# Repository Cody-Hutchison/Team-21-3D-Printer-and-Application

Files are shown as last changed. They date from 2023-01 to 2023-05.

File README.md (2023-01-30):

# Team-21-3D-Printer-and-Application

Currently 3D Printers require users to manually upload a G-code file by and external storage device and initiate the printing process via controls on the printer. Our goal is to create a 3D printer that you ance upload, control, initiate, and interupt the 3D printing process from anywhere in the world that you have internet access. We also want to keep the print time be within 10% of the printing time of the Ender 3 which is the frame and mechanical hardware used for our printer. To try to increase the print time we are going to attempt it by speading up the Z-axis movement speed.

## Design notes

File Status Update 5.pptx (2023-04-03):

## Team 21: 3D Printer and Application Interface Bi-Weekly Update 5 Cody Hutchison Steven Liu Abigail Morar Sponsor: Dalton Cyr TA: Milenka Gamero

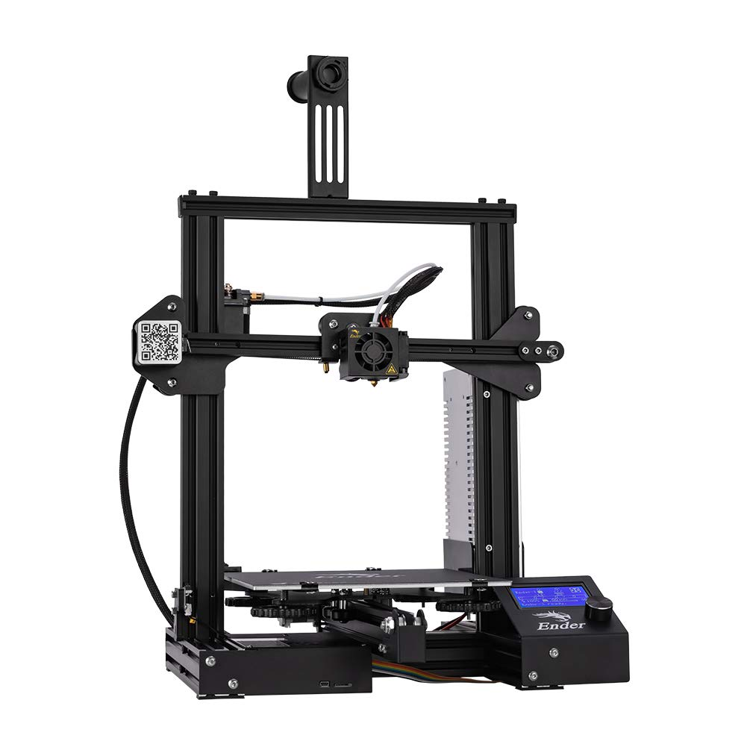
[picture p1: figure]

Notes: Michelle

## Project Summary

- Current 3D printers require the user to manually upload a G-code file by an external storage device and initiate the printing process via controls on the printer
- The new 3D printer and Application will allow the uploading, controlling, and initiation of printing from anywhere with internet access. The print time will also be within 10% of the Ender 3 printing time while also attempting to speed up the Z-axis movement speed.

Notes: Kyle

## Project/Subsystem Overview

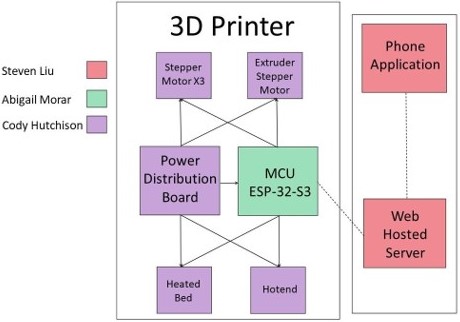
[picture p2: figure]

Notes: Eric

## Project Changes for 404

Everything is still on track from what was planned in 403.
As of now, changes are mostly geared towards fixing bugs in the subsystems for full integration, and dealing with whatever problems may arise from that.

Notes: Eric

## Project Timeline

Validate System

Finish Subsystems

Integrate Subsystems

Final Presentation

Final Demo

April 24

February 15

March 29

April 10

March 15

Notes: January 30th - February 5th
Ensure all parts required to complete PCBs are on hand or order more
Start populating PCB if they have arrived
February 6th - 12th
Have PCB populated and validate

## Electrical Subsystem Cody Hutchison

Accomplishments since last update 24 hrs of effort | Ongoing progress/problems and plans until the next presentation
| Integrate PCB with MCU Build printer case for PCBs Solder jumper wires and modify board for the axis switches

## Electrical Subsystem Cody Hutchison

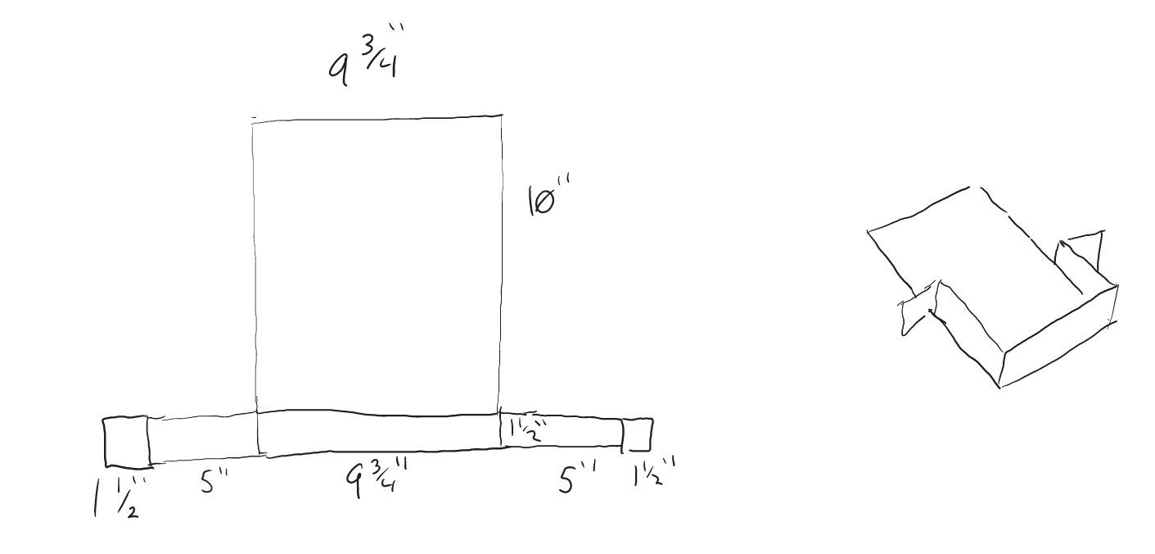
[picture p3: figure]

## Application and Server Subsystem Steven Liu

Accomplishments since last update 15 hrs of effort | Ongoing progress/problems and plans until the next presentation
Application tuning Added logo and splash screen | Look for possible improvements Finish poster Update Final Report

## Application and Server Subsystem Steven Liu

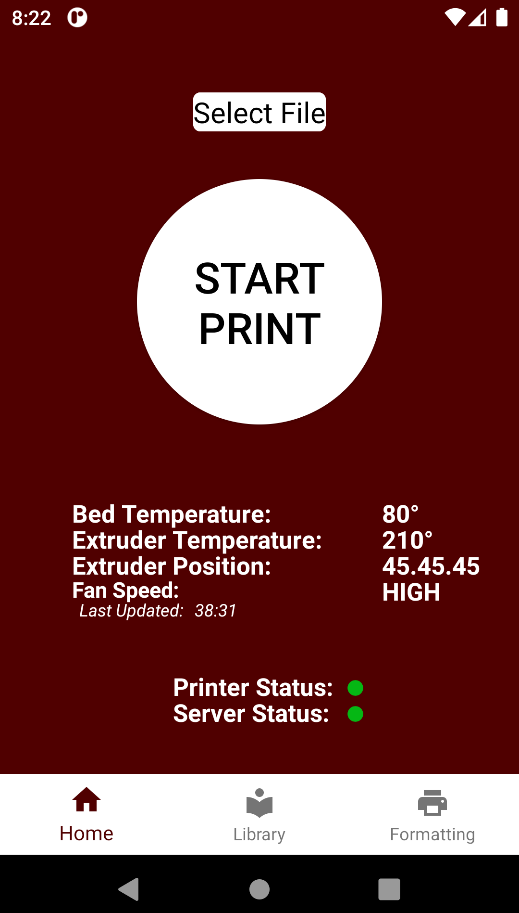
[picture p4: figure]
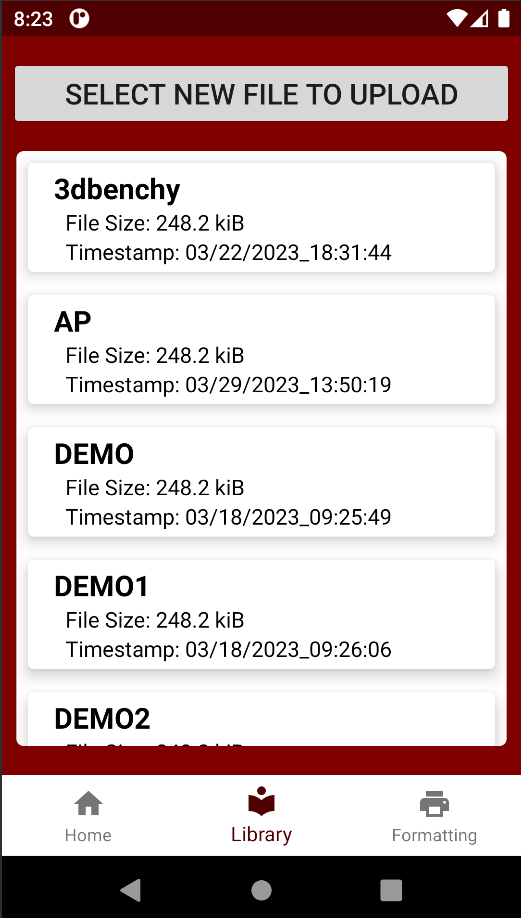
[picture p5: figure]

## Microcontroller Programming Subsystem Abigail Morar

Accomplishments since last update 20 hrs of effort | Ongoing progress/problems and plans until the next presentation
- Heated bed reading/writing and maintaining temperature correctly - Found steps per full revolution for each motor - Found mm per full revolution and steps/mm | - Measure/calculate constants for hotend - Verify all motor speeds for print and extruding amount per mm with filament - Updating changes to main code - Tweaking for accuracy

## Microcontroller Programming Subsystem Abigail Morar

## Integration

Accomplishments since last update | Ongoing progress/problems and plans until the next presentation
Continue integration between MCU and Electrical Subsystem | Validate App/Server and MCU integration Validate MCU and Electrical Subsystem integration

## Parts Ordering Status

- No parts on order or required at the moment

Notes: Michelle

## Execution Plan

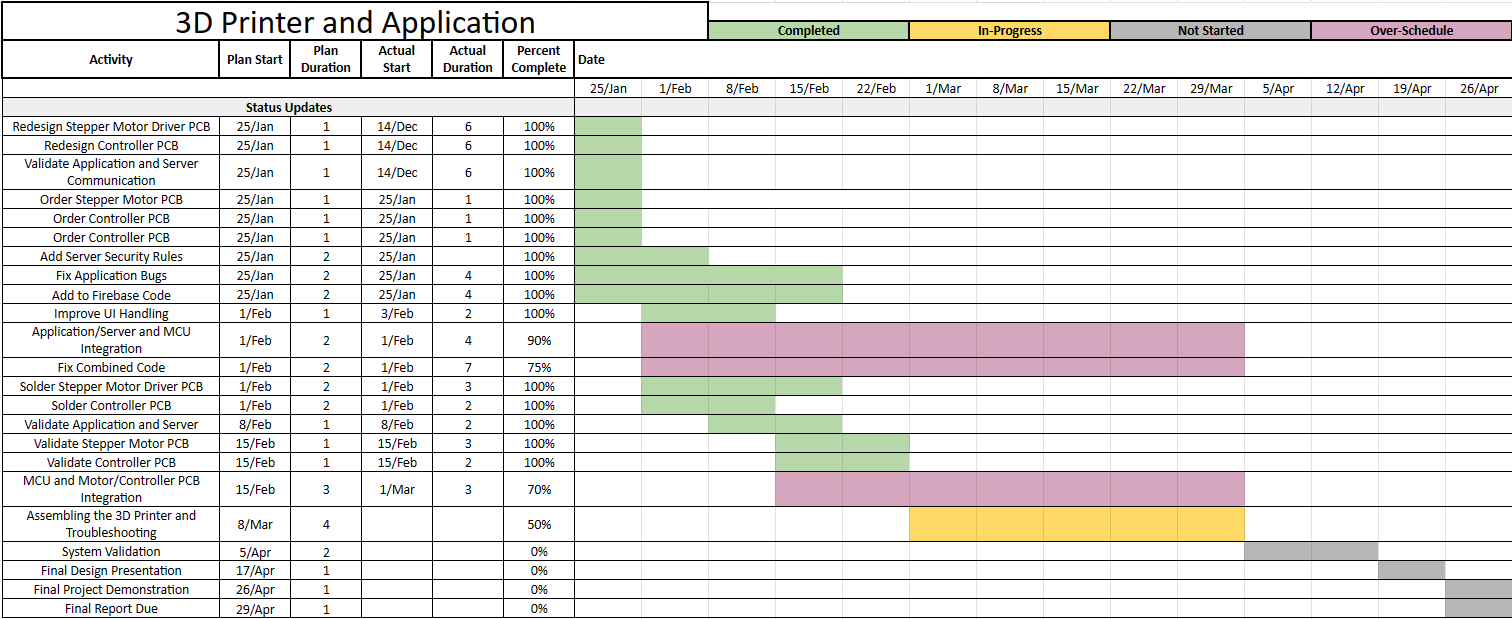
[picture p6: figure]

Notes: Michelle

## Validation Plan

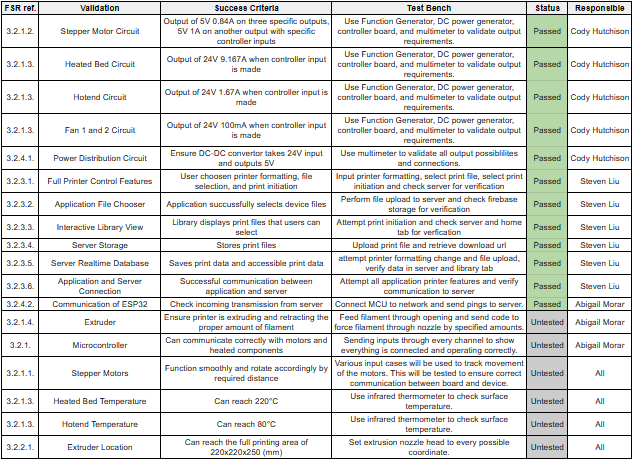
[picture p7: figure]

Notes: Michelle

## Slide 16

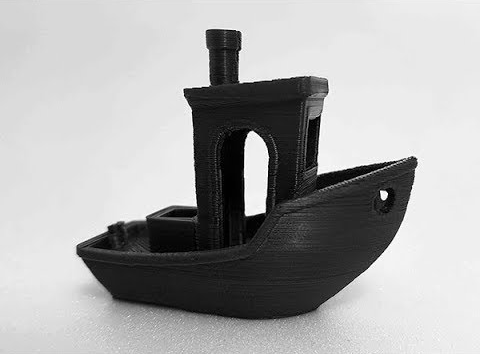
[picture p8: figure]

Questions? Comments?
Thank You

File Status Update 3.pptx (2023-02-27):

## Team 21: 3D Printer and Application Interface Bi-Weekly Update 3 Cody Hutchison Steven Liu Abigail Morar Sponsor: Dalton Cyr TA: Milenka Gamero


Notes: Michelle

## Project Summary

- Current 3D printers require the user to manually upload a G-code file by an external storage device and initiate the printing process via controls on the printer
- The new 3D printer and Application will allow the uploading, controlling, and initiation of printing from anywhere with internet access. The print time will also be within 10% of the Ender 3 printing time while also attempting to speed up the Z-axis movement speed.

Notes: Kyle

## Project/Subsystem Overview


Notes: Eric

## Project Changes for 404

Everything is still on track from what was planned in 403.
As of now, changes are mostly geared towards fixing bugs in the current subsystems, preparing for full integration, and dealing with whatever problems may arise from that.

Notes: Eric

## Project Timeline

Validate System

Finish Subsystems

Integrate Subsystems

Final Presentation

Final Demo

April 24

February 15

March 29

April 10

March 15

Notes: January 30th - February 5th
Ensure all parts required to complete PCBs are on hand or order more
Start populating PCB if they have arrived
February 6th - 12th
Have PCB populated and validate

## Electrical Subsystem Cody Hutchison

Accomplishments since last update 22 hrs of effort | Ongoing progress/problems and plans until the next presentation
- Validated Main Controller PCB - Validated Axis Driver PCB | Integrate PCB with MCU Design printer mount for PCBs

## Electrical Subsystem Cody Hutchison

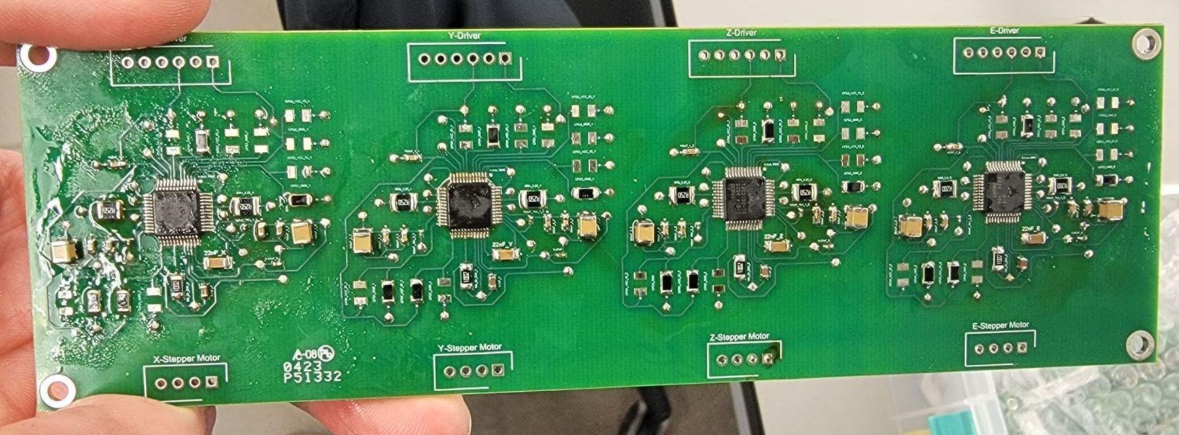
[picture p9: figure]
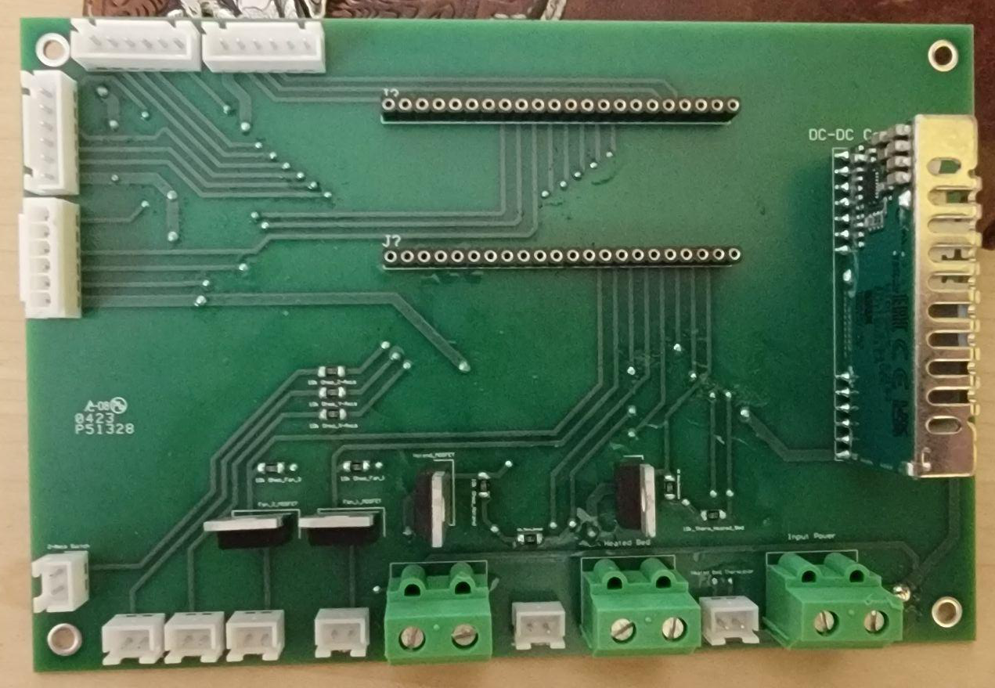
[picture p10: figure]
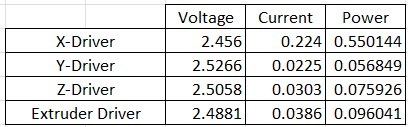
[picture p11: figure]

## Application and Server Subsystem Steven Liu

Accomplishments since last update 10 hrs of effort | Ongoing progress/problems and plans until the next presentation
Fixed url firebase communication bug Fixed in-app fragment communication bugs | Add a print completion notification to user Make a new demo recording using app from physical device Look for other possible bugs or UI improvements

## Application and Server Subsystem Steven Liu

## Microcontroller Programming Subsystem Abigail Morar

Accomplishments since last update 11 hrs of effort | Ongoing progress/problems and plans until the next presentation
- Completed integration with Firebase | - Will begin testing functionality of stepper motors and integrate with PCB

## Integration

Accomplishments since last update | Ongoing progress/problems and plans until the next presentation
App/Server and MCU subsystems integrated | Validate App/Server and MCU integration Begin integration between MCU and Electrical Subsystem

## Parts Ordering Status

- 3 TMC-2130 Driver Controller were ordered and received

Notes: Michelle

## Execution Plan

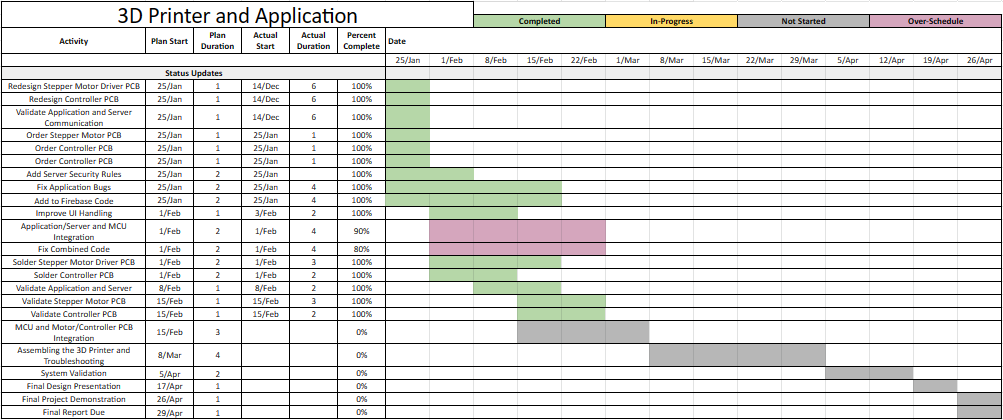
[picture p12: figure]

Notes: Michelle

## Validation Plan


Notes: Michelle

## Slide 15


Questions? Comments?
Thank You

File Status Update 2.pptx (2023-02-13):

## Team 21: 3D Printer and Application Interface Bi-Weekly Update 2 Cody Hutchison Steven Liu Abigail Morar Sponsor: Dalton Cyr TA: Milenka Gamero


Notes: Michelle

## Project Summary

- Current 3D printers require the user to manually upload a G-code file by an external storage device and initiate the printing process via controls on the printer
- The new 3D printer and Application will allow the uploading, controlling, and initiation of printing from anywhere with internet access. The print time will also be within 10% of the Ender 3 printing time while also attempting to speed up the Z-axis movement speed.

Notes: Kyle

## Project/Subsystem Overview


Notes: Eric

## Project Changes for 404

Everything is still on track from what was planned in 403.
As of now, changes are mostly geared towards fixing bugs in the current subsystems, preparing for full integration, and dealing with whatever problems may arise from that.

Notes: Eric

## Project Timeline

Validate System

Finish Subsystems

Integrate Subsystems

Final Presentation

Final Demo

April 24

February 15

March 29

April 10

March 15

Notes: January 30th - February 5th
Ensure all parts required to complete PCBs are on hand or order more
Start populating PCB if they have arrived
February 6th - 12th
Have PCB populated and validate

## Electrical Subsystem Cody Hutchison

Accomplishments since last update 12 hrs of effort | Ongoing progress/problems and plans until the next presentation
- Assembling PCBs | Validate both PCBs Integrate PCB with MCU Design printer mount for PCBs

## Electrical Subsystem Cody Hutchison

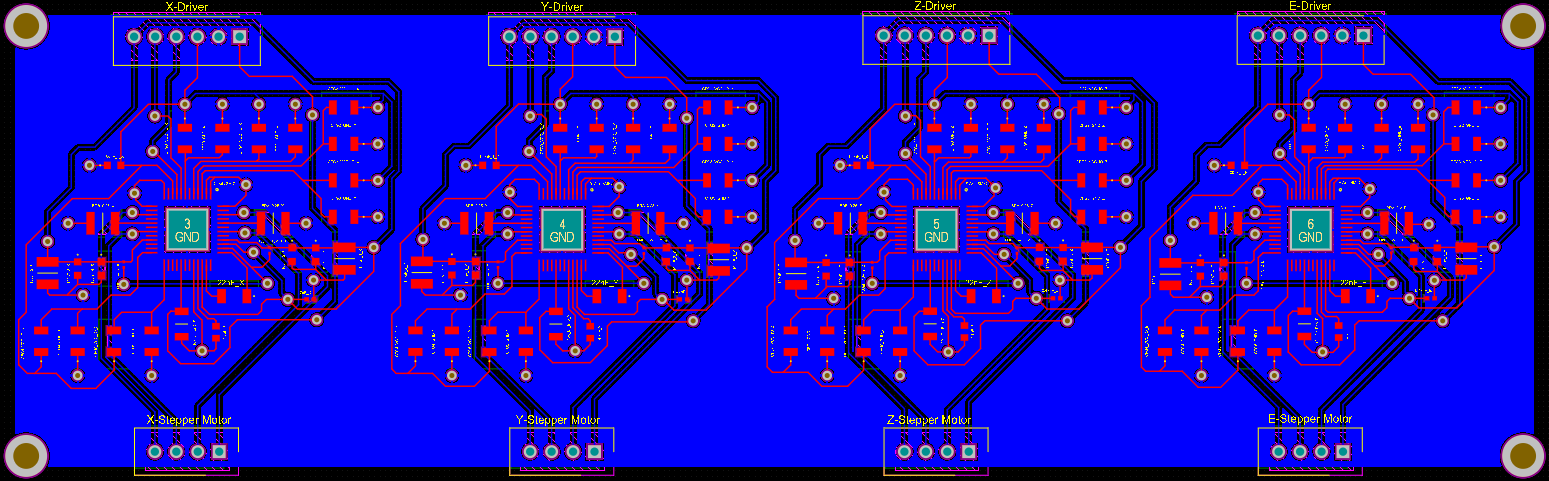
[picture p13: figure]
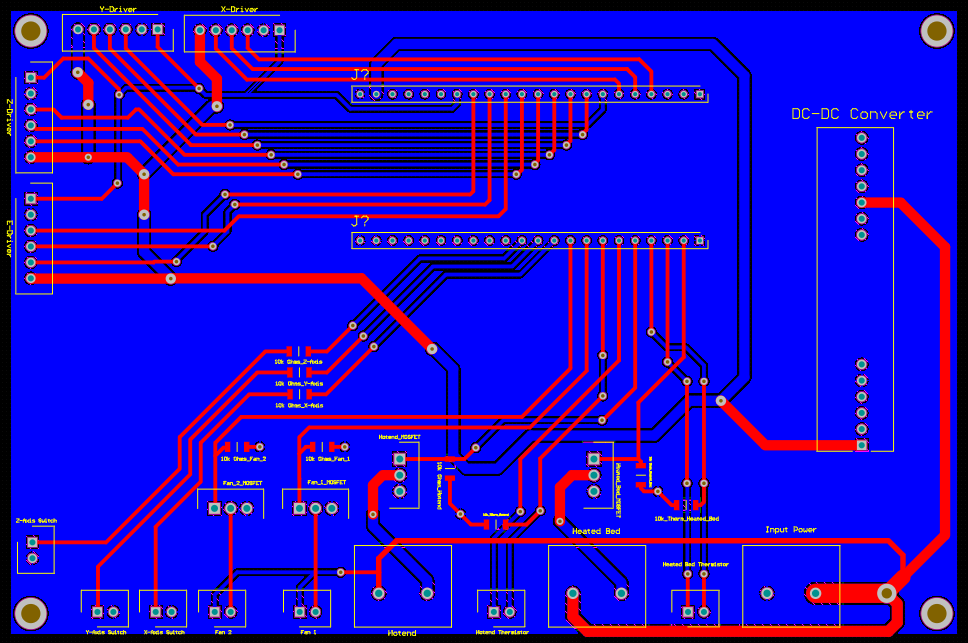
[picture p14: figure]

## Application and Server Subsystem Steven Liu

Accomplishments since last update 25 hrs of effort | Ongoing progress/problems and plans until the next presentation
- Fixed display bug using Android SharedViewModel class - Fixed bug that would freeze and crash app on file upload cancellation - Working on using Firebase Functions to work around url communication bug | - Be ready for adjustments while integrating MCU - Fix url firebase communication bug - Look for other possible bugs or UI improvements

## Application and Server Subsystem Steven Liu

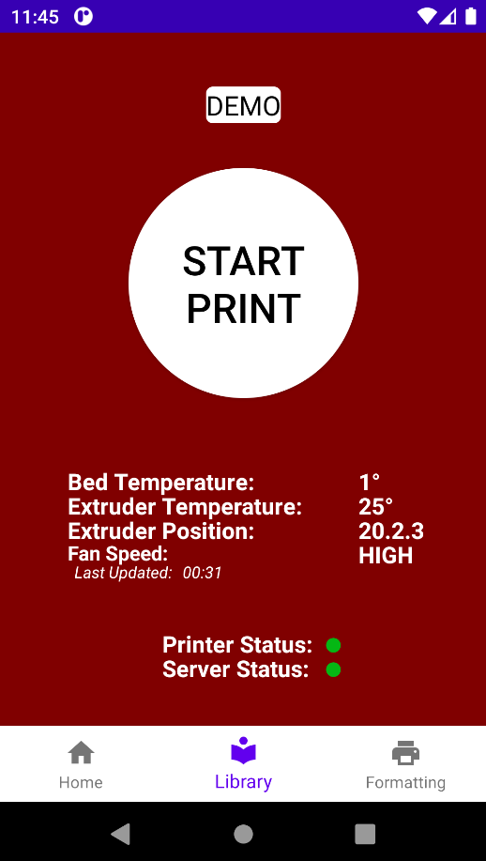
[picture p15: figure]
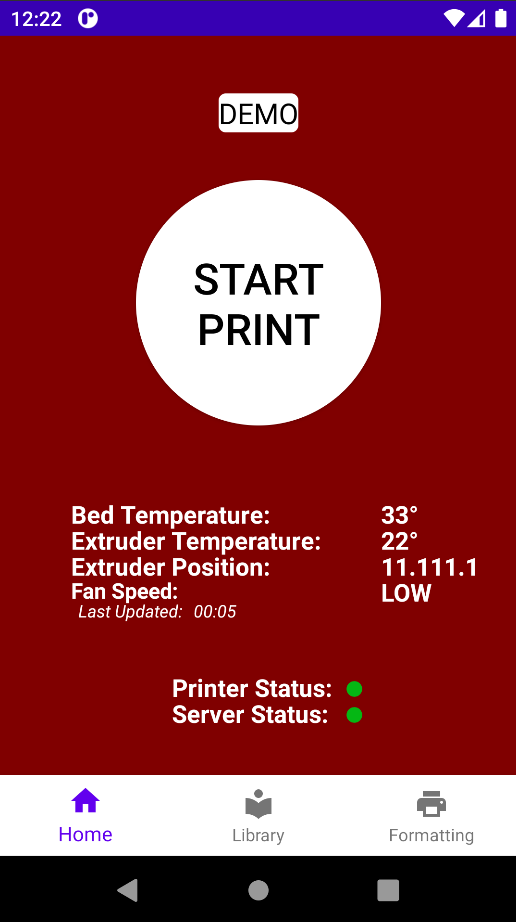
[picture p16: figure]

Display Bug Fixed

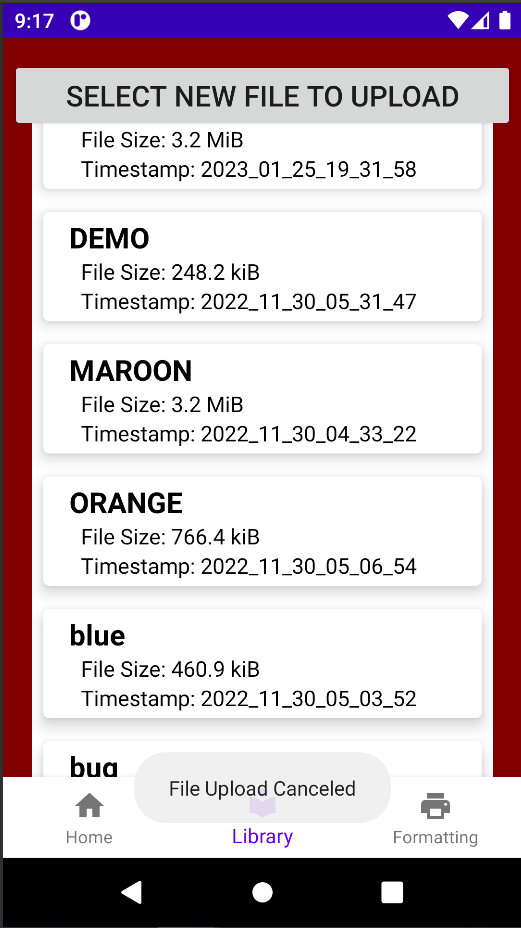
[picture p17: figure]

Cancel Upload Bug Fixed

Display Bug

## Microcontroller Programming Subsystem Abigail Morar

Accomplishments since last update 12 hrs of effort | Ongoing progress/problems and plans until the next presentation
- Began integration with Firebase server - Can write to correct path in Firebase | - Finishing up integration with the server to validate phone app communication - Will begin testing functionality of stepper motors and other components

## Parts Ordering Status

- All planned parts have been ordered and received

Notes: Michelle

## Execution Plan

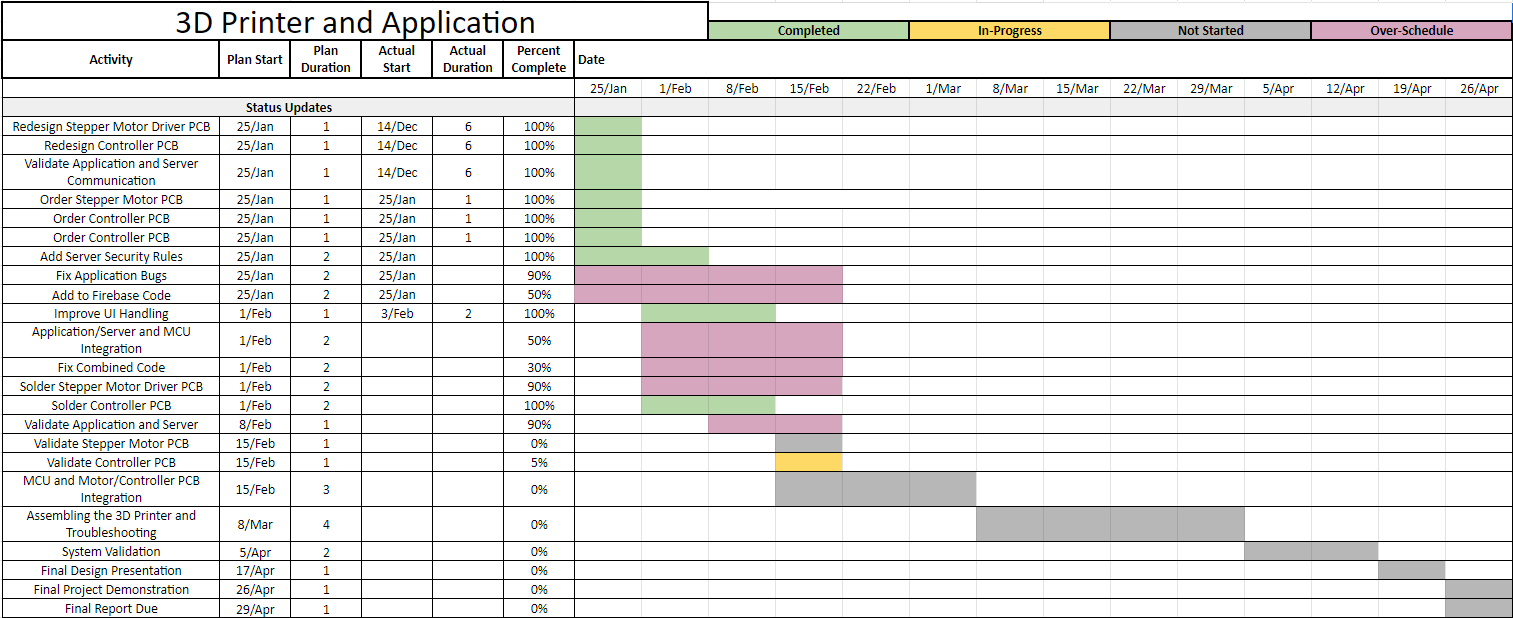
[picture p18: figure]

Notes: Michelle

## Validation Plan

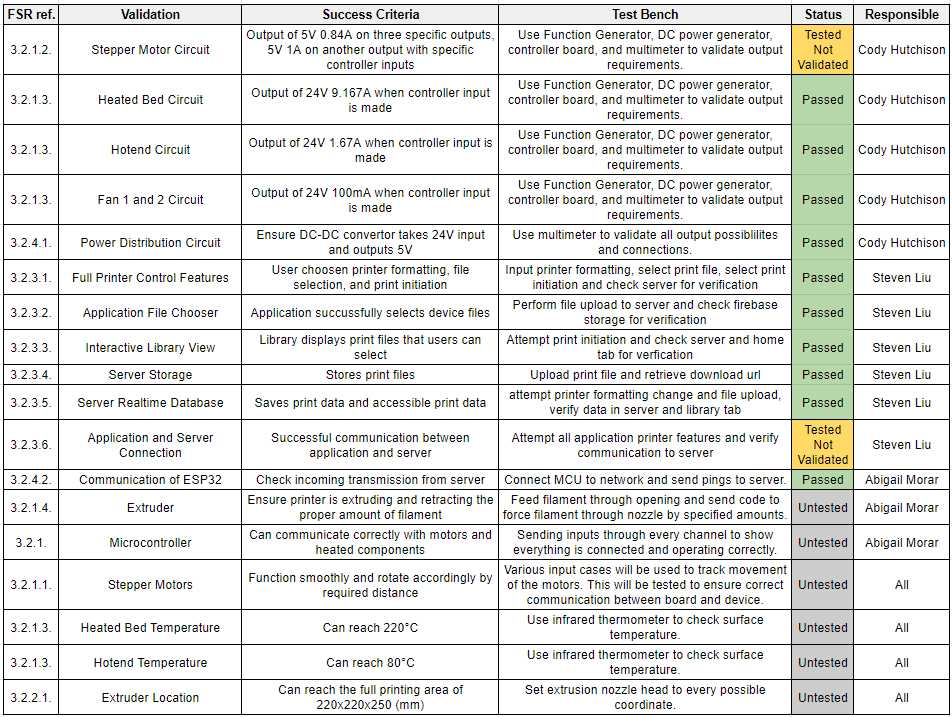
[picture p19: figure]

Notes: Michelle

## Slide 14


Questions? Comments?
Thank You

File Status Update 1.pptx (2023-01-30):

## Team 21: 3D Printer and Application Interface Bi-Weekly Update 1 Cody Hutchison Steven Liu Abigail Morar Sponsor: Dalton Cyr TA: Milenka Gamero


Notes: Michelle

## Project Summary

- Current 3D printers require the user to manually upload a G-code file by an external storage device and initiate the printing process via controls on the printer
- The new 3D printer and Application will allow the uploading, controlling, and initiation of printing from anywhere with internet access. The print time will also be within 10% of the Ender 3 printing time while also attempting to speed up the Z-axis movement speed.

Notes: Kyle

## Project/Subsystem Overview


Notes: Eric

## Project Changes for 404

Everything is still on track from what was planned in 403.
As of now, changes are mostly geared towards fixing bugs in the current subsystems, preparing for full integration, and dealing with whatever problems may arise from that.

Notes: Eric

## Project Timeline

Validate System

Finish Subsystems

Integrate Subsystems

Final Presentation

Final Demo

April 24

February 15

March 29

April 10

March 15

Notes: January 30th - February 5th
Ensure all parts required to complete PCBs are on hand or order more
Start populating PCB if they have arrived
February 6th - 12th
Have PCB populated and validate

## Electrical Subsystem Cody Hutchison

Accomplishments since 403 55 hrs of effort | Ongoing progress/problems and plans until the next presentation
- Redesigned and corrected errors with the the Stepper Motor Driver PCB. - Minor modifications to the Controller PCB due to a header component used to plug the MCU being incorrect - Placed order for new PCB boards | - Populate both PCBs - Validate both PCBs

## Electrical Subsystem Cody Hutchison

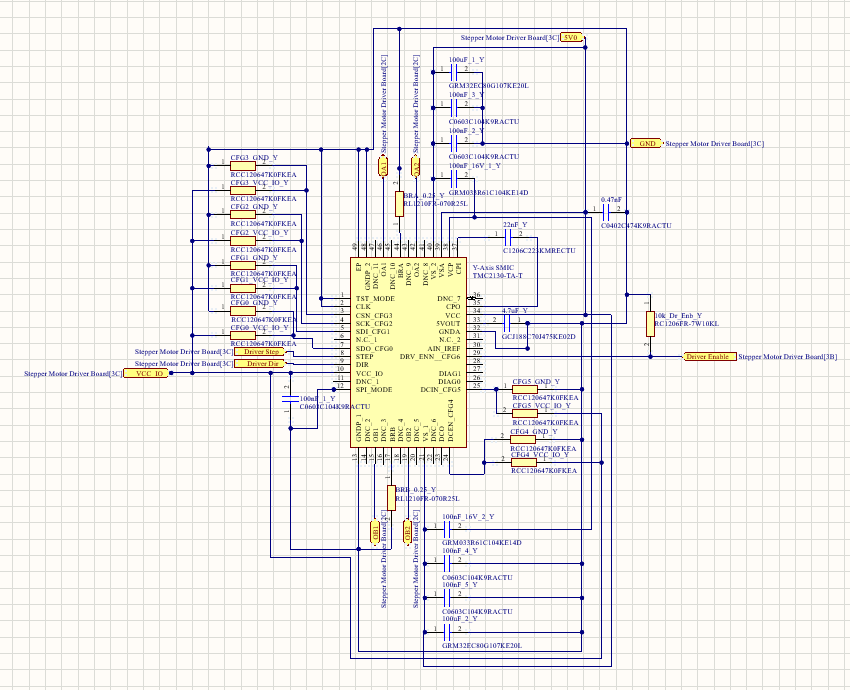
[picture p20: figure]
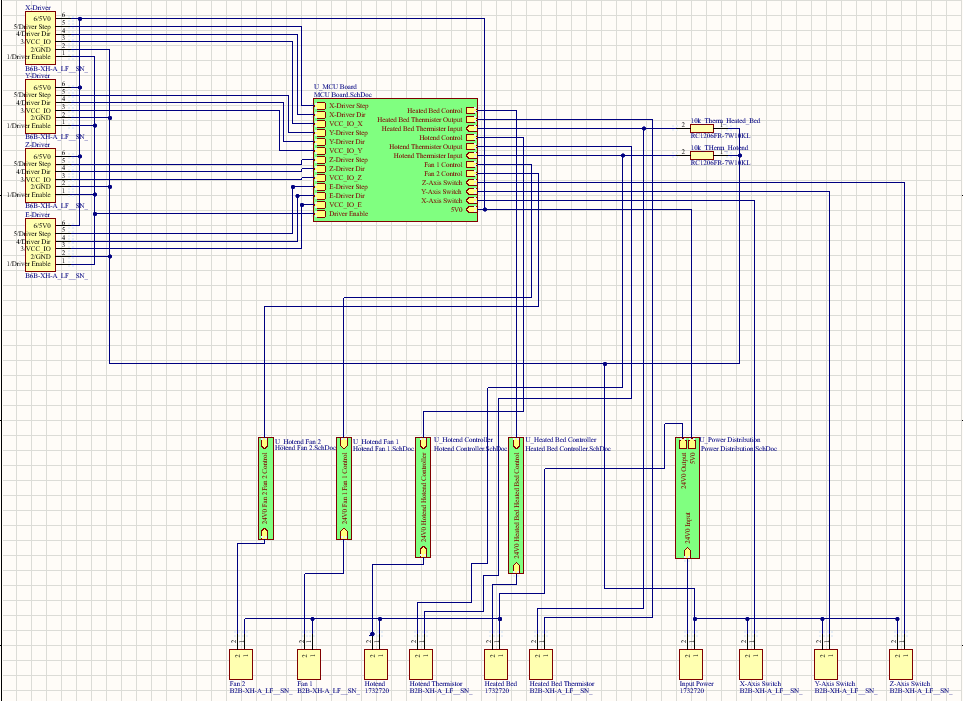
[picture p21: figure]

## Application and Server Subsystem Steven Liu

Accomplishments since 403 15 hrs of effort | Ongoing progress/problems and plans until the next presentation
- Added security rules to server - Improved application UI - Incorporating Android SharedViewModel class to fix bug | - Finish incorporating SharedViewModel class to app and validate - Work on fixing other bug - Find other possible UI improvements - Work on connecting with MCU subsystem

## Application and Server Subsystem Steven Liu

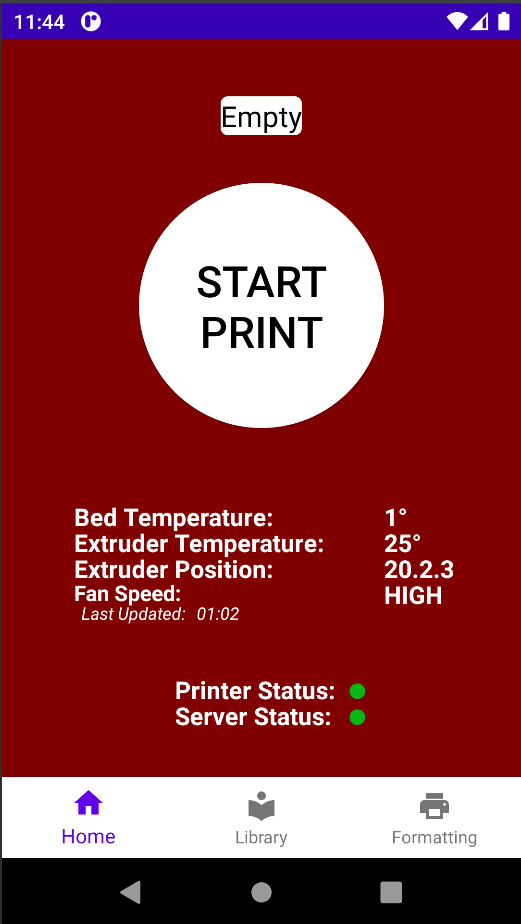
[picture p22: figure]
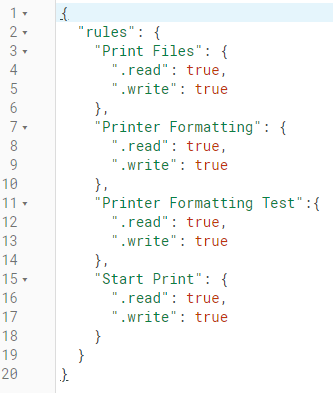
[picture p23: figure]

## Microcontroller Programming Subsystem Abigail Morar

Accomplishments since 403 10 hrs of effort | Ongoing progress/problems and plans until the next presentation
- Ensured all code still works and can connect to server - Combined code | - Fix bug with reading from Firebase and other issues - Adding code to check for updates from phone app to interrupt G-code reading process, update, then resume or cancel - Waiting on integration with motors to calculate the steps to mm

## Parts Ordering Status

  - PCBs are currently on order
  - Order PCB components

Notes: Michelle

## Execution Plan

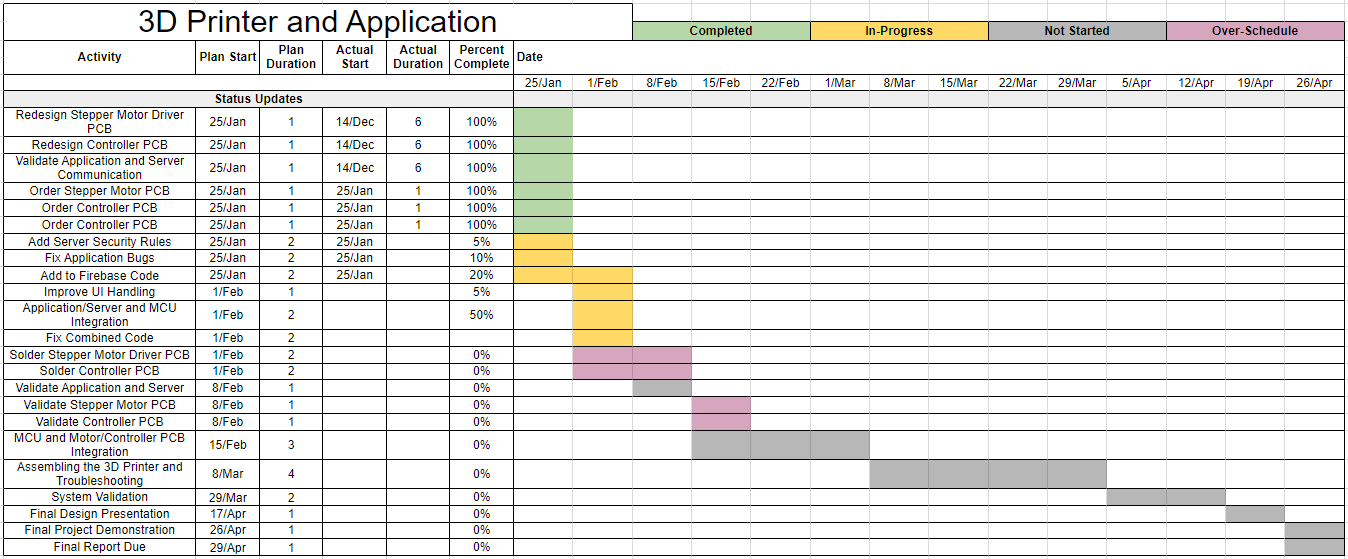
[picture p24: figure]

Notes: Michelle

## Validation Plan


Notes: Michelle

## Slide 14


Questions? Comments?
Thank You

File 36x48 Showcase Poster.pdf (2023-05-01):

### Outcomes

The printer communicates to the phone application via Wi-Fi and can be controlled remotely by the user. Control from the app includes setting extruder location, fan power, and heated bed and hotend temperatures. The MCU executes these commands and sends updates back to the app for real-time user verification. The application parses and uploads G-code files to the database as well provides user ability to start and cancel prints. The PCBs currently work as expected. This is the 2nd iteration of the designs and had to make a few minor corrections on main controller board by soldering wires as jumpers and isolating 3 separate pins from the ground plane.

### Engineering Analysis

The mobile application, server, and MCU work together to provide an intuitive user interface and allow remote communication. While the MCU and PCB work together to perform all physical operations of the 3D printer. All user inputs are communicated from the application to the server, which provides a database and storage for handling all pertinent information that can then be read by the MCU. The stepper motor controller PCB provides control over the stepper motors on the 3D printer.

# 3D Printer and Phone Application

## Cody Hutchison, Steven Liu, Abigail Morar Dalton Cyr

Current | Issues

The 3D printer will run through the G-code and attempt to print an item, but is currently only printing on one quadrant of the heated bed. Another part of the issue is the extruder isn’t pushing enough filament out to properly print.

Figure 1. 3D Printer System Overview

### Problem Definition

Current 3D printers require the user to manually upload a G-code file by an external storage device and initiate the printing process via controls on the printer.

### Methodology

This 3D printer project was divided into 3 subsystems: • Electronics – Main controller and

Stepper Motor Controller Printed Controller Boards (PCBs) • Microcontroller Unit (MCU) • User Interface - Phone Application and

Server
Integration between the subsystems were solved with the MCU being mounted directly to the main controller PCB and the phone application communicating to the MCU through the web-hosted server.

### Impact

There are many benefits of having a 3D printer that is controlled by a phone application over a Wi-Fi network whether it’s for commercial or consumer use. • Gives access to the 3D printer to people

who aren’t technologically inclined

- Initiating print when away from the office, on a business trip, or working from home
- Permits printing while busy with other tasks around the house or office
- Allows a person to be more social and not confined to their home

References

### 1. Ender 3 Printer Manual 2. ESP32-S3 Datasheet 3. TMC-2130 Datasheet 4. IEEE 802.11-2020

### 5. Android Documentation Acknowledgements

We would like to express gratitude to Dr. John Lusher of the Electrical Engineering Department for his assistance in this project.

# EPS Booth: 302

The MCU analyzes and computes signals from the PCB to send information to the application. The MCU parses incoming G-code lines and relays heated component temperatures, extruder location, and fan and print completion status back to the user.

Table 1. Main Controller PCB Data

Table 2. Stepper Motor Power Usage

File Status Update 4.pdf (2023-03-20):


# Team 21: 3D Printer and Application Interface Bi-Weekly Update 4

### Cody Hutchison Steven Liu Abigail Morar Sponsor: Dalton Cyr TA: Milenka Gamero

# Project Summary

- Current 3D printers require the user to manually upload a G-code file by an external storage device and initiate the printing process via controls on the printer - The new 3D printer and Application will allow the uploading, controlling, and initiation of printing from anywhere with internet access. The print time will also be within 10% of the Ender 3 printing time while also

attempting to speed up the Z-axis movement speed.

# Project/Subsystem Overview


# Project Changes for 404

### Everything is still on track from what was

planned in 403.

### As of now, changes are mostly geared towards fixing bugs in the current

subsystems, preparing for full integration,

### and dealing with whatever problems may

arise from that.

# Project Timeline

February 15; March 15; March 29; April 10; April 24; Finish Subsystems; Integrate Subsystems; Validate System; Final Presentation; Final Demo

# Electrical Subsystem

Cody Hutchison
Accomplishments since last update 16 hrs of effort | Ongoing progress/problems and plans until the next presentation
| - Integrate PCB with MCU - Design printer case for PCBs

# Electrical Subsystem


Cody Hutchison

# Application and Server Subsystem

Steven Liu
Accomplishments since last update 10 hrs of effort | Ongoing progress/problems and plans until the next presentation
- Application tuning - Added print completion notification | - Look for possible improvements

# Application and Server Subsystem


Steven Liu

# Microcontroller Programming Subsystem

Abigail Morar
Accomplishments since last update 53 hrs of effort | Ongoing progress/problems and plans until the next presentation
- Began integration with Electrical Subsystem - Full communication to fans, heated components, and stepper motors - Full control of fans and heated bed | - Value constants for hotend - steps/mm, and steps/rev, speed - ensure all parts are functioning as designed before validation across all subsystems

# Integration

Accomplishments since last update | Ongoing progress/problems and plans until the next presentation
- Began integration between MCU and Electrical Subsystem | - Validate App/Server and MCU integration - Validate MCU and Electrical Subsystem integration

# Parts Ordering Status

## - No Parts on Order

# Execution Plan


# Validation Plan


# Questions? Comments? Thank You

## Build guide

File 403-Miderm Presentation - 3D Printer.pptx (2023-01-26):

## 3D Printer and Application Interface Cody Hutchison Steven Liu Abigail Morar


## Executive Summary

- Problem Statement
  - Current 3D printers require the user to manually upload a G-code file by an external storage device and initiate the printing process via controls on the printer
- Solution
  - The new 3D printer and Application will allow the uploading, controlling, and initiation of printing from anywhere with internet access
  - Quicker Z-axis motion
  - Print time within 10% of a regular Ender 3 Printer

## System Overview

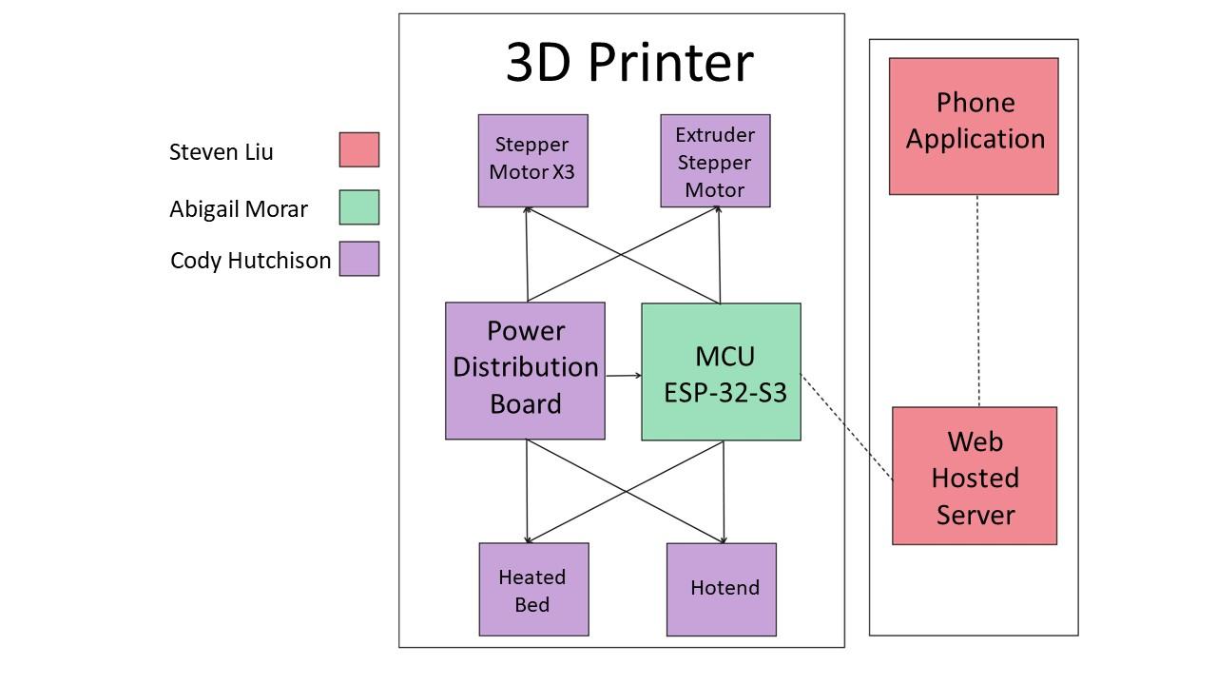
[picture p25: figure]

## Task Partition

- Abigail: Program ESP32-S3
- Cody: Design power distribution board, stepper motor, hotend, and heated bed controllers
- Steven: Design and program the application and web hosted server

## Electrical System Overview

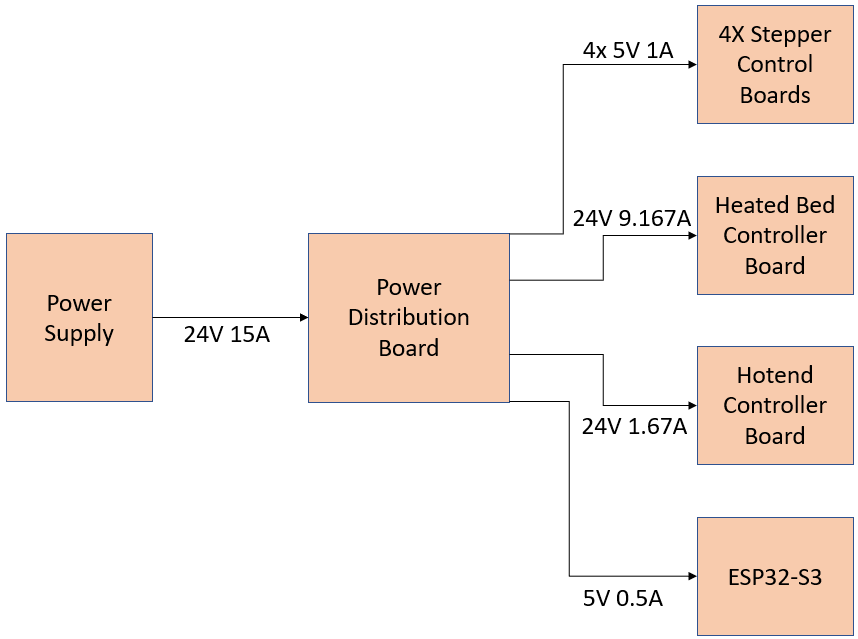
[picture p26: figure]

## Electrical System Overview

- Power Distribution
  - Split 24V 15A into four 5V 1A outputs, a 5V 0.5A output, a 24V 9.167A output, and a 24V 1.67A output
- Stepper Motor Drivers
  - Design 4 stepper motors drivers to control
  - Three at 5V 0.84A and one at 5V 1A
- Hotend
  - N-Type MOSFET that takes MCU inputs and allows 24V 9.167A through
- Heated Bed
  - N-Type MOSFET that takes MCU inputs and allows 24V 1.67A through

## Microcontroller Unit

- ESP32-S3
- Connects all subsystems
- Communicates to server
- Controls all printer components

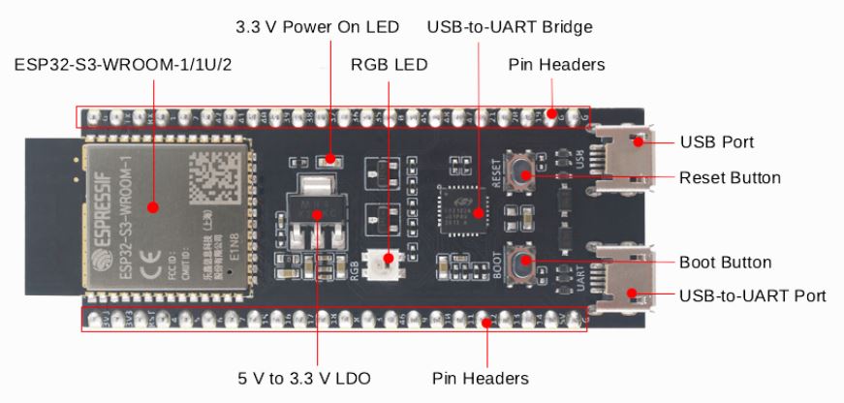
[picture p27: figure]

## MCU Coding

- Programmed in C
- Reads in user input and files from application
- Translates G-code to printer
- Controls heating elements and stepper motors
- Drives extruder
- Links device to the internet

## Phone Application

- Perform all the tasks of the original software
- Developed in Android Studio using Kotlin Programming Language

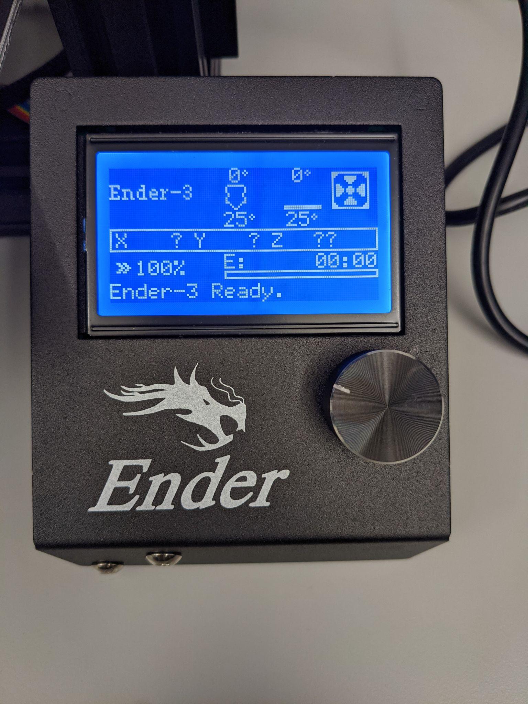
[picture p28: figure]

Printer Name

Select Print

Bed Temperature 0°
Extruder Temperature 0°
Extruder Position 0.0.0
Fan Speed 0
Last updated: 0s

Printer Status:
Server Status:

Start Print

## Server

- Intercommunication between mobile application and physical printer
- Stores a library of previous prints

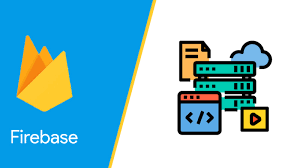
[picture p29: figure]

## User Interface Model

Printer Name

model_bridge

Bed Temperature 0°
Extruder Temperature 0°
Extruder Position 0.0.0
Fan Speed 0
Last updated: 0s

Printer Status:
Server Status:

Printer Name

Select Print

Bed Temperature 0°
Extruder Temperature 0°
Extruder Position 0.0.0
Last updated: 0s

Printer Status:
Server Status:

Printer Settings

Revert

Print Library

Upload Print to Library

Select Print File

Search Library

model_ship

model_plane

Skeleton_hand

mini_whale

Print

Print Library

Upload Print to Library

Select Print File

Select Print File

Select from Files

Select from Library

Search Library

model_ship

model_plane

Skeleton_hand

mini_whale

Print

Printer Settings

Print Library

Settings

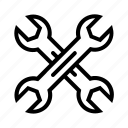
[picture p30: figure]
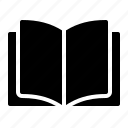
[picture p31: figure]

Bed Temperature

Extruder Temperature

Home Position

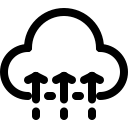
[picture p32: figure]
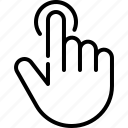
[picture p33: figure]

Printing
18%

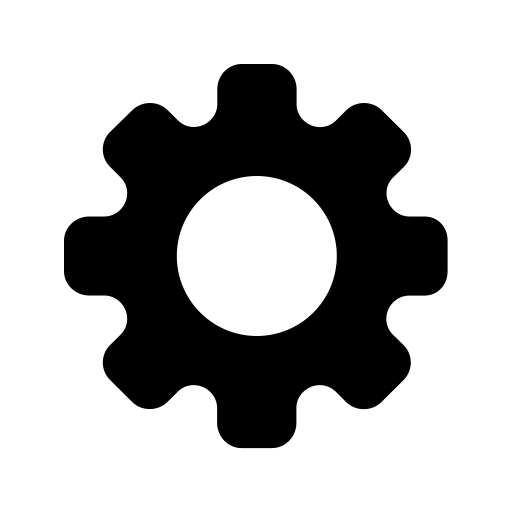
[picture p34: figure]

Start Print

## Execution Plan

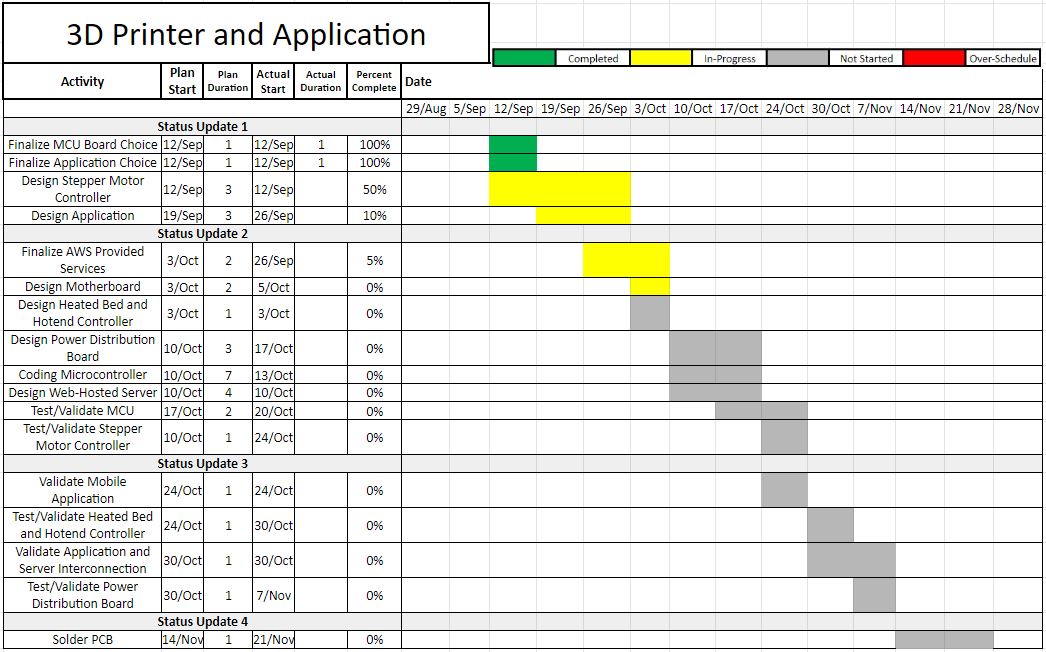
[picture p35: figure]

## Validation Plan

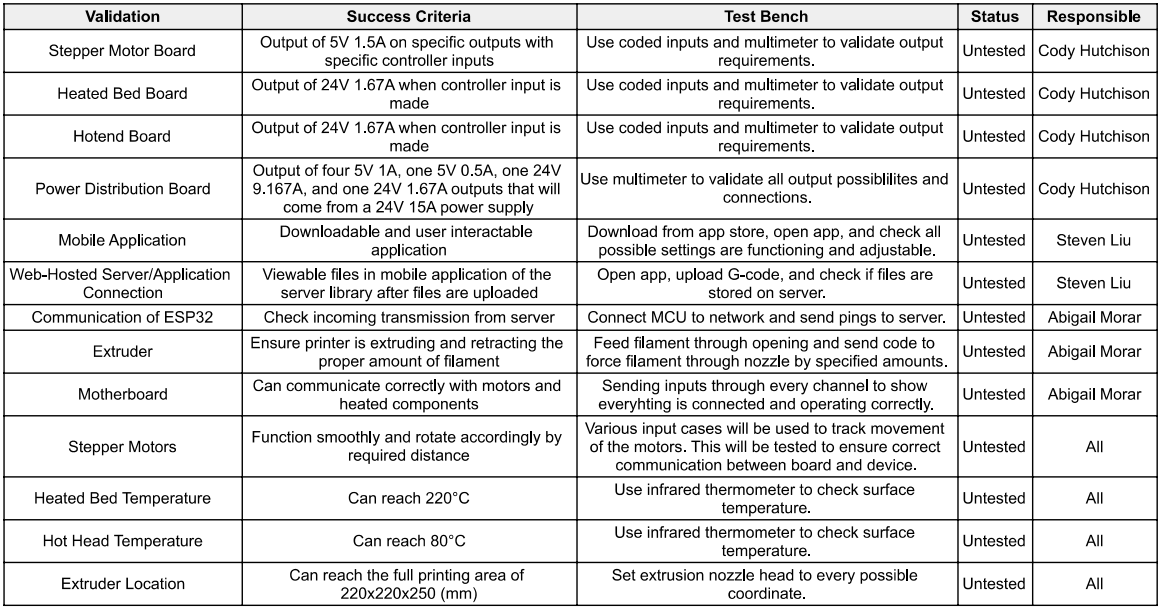
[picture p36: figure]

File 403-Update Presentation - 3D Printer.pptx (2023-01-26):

## 3D Printer and Application Interface Cody Hutchison Steven Liu Abigail Morar


## Executive Summary

- Problem Statement
  - Current 3D printers require the user to manually upload a G-code file by an external storage device and initiate the printing process via controls on the printer
- Solution
  - The new 3D printer and Application will allow the uploading, controlling, and initiation of printing from anywhere with internet access
  - Quicker Z-axis motion
  - Print time within 10% of a regular Ender 3 Printer

## System Overview


## Task Partition

- Abigail: Program ESP32-S3
- Cody: Design and build the Electrical Systems
- Steven: Design and program the application and web hosted server

## Electrical System Update

Accomplishments since the last presentation ~40hrs
Finished design of Stepper Motor Controllers and Power Distribution Started Schematics and PCB design Ordered major components including Stepper Motor Driver IC and DC-DC converter
Ongoing progress/problems and plans until the next presentation
Minor issue with the hot end and heated bed controlling with MOSFETs requiring a Digital-to-Analog converter Project going over budget Continue design of the schematics and PCB

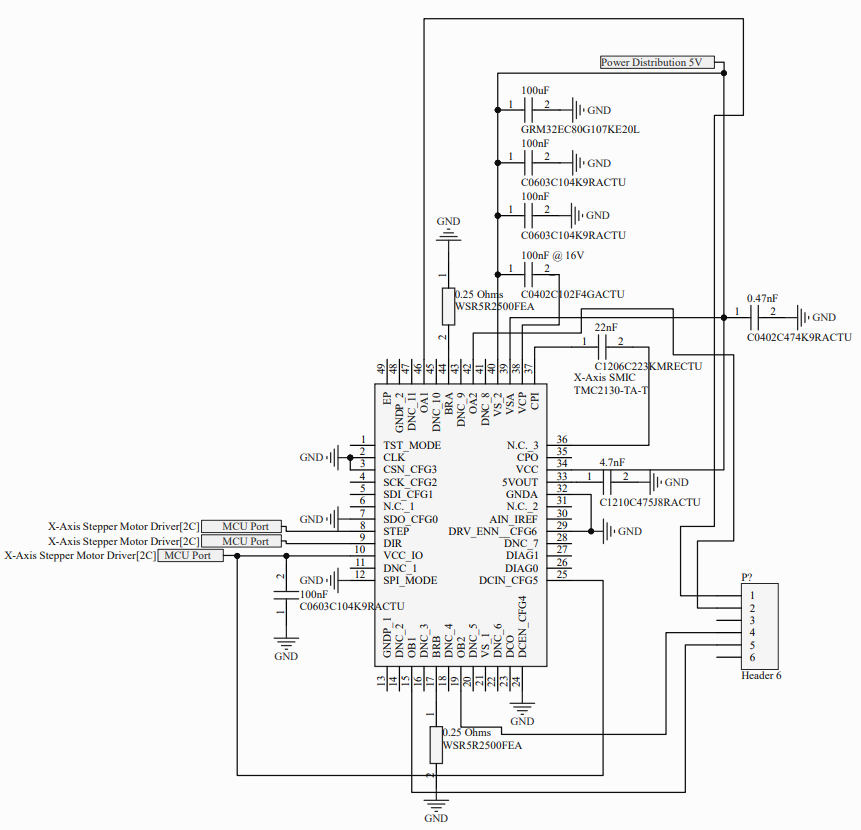
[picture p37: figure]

## MCU Coding Update

Accomplishments since the last presentation ~15hrs
Setup Espressif IDE Set auto home and build volume parameters Reads in hard coded G-code files Stores lines of code in array Updates XYZ axis locations and extrusion amount
Ongoing progress/problems and plans until the next presentation
Finish converting G-code into C Controlling heated components and motors Communicating with phone application WiFi connection

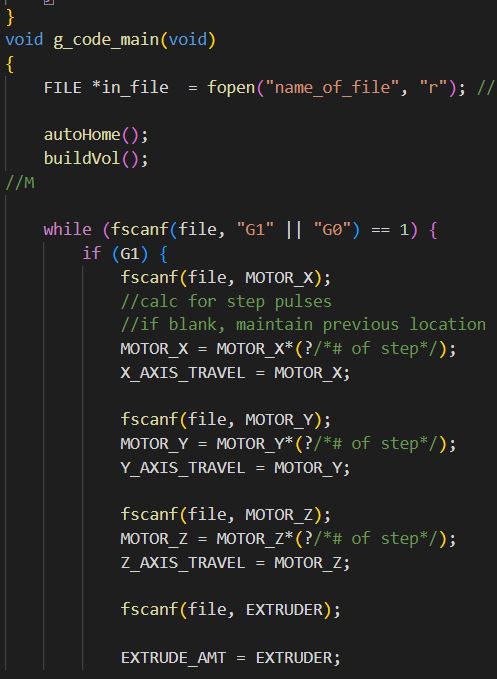
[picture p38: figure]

## Phone Application and Server Update

Accomplishments since the last presentation ~20hrs
Finished App Navigation design Established communication between fragments (tab/pages) Connected application to Firebase, set up dependencies Set up firebase realtime database
Ongoing progress/problems and plans until the next presentation
Finish adding all UI features to application Establishing simple communication to firebase server and view database in scrollview (visual library of files)

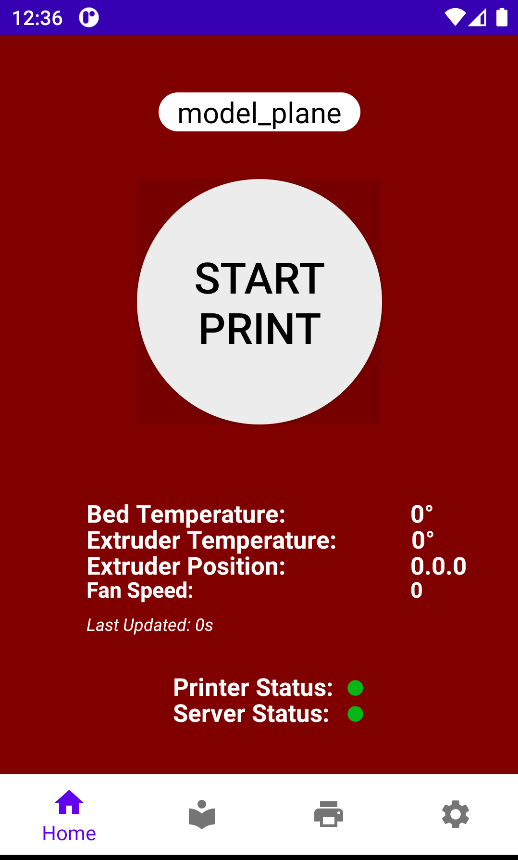
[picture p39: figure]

## Execution Plan

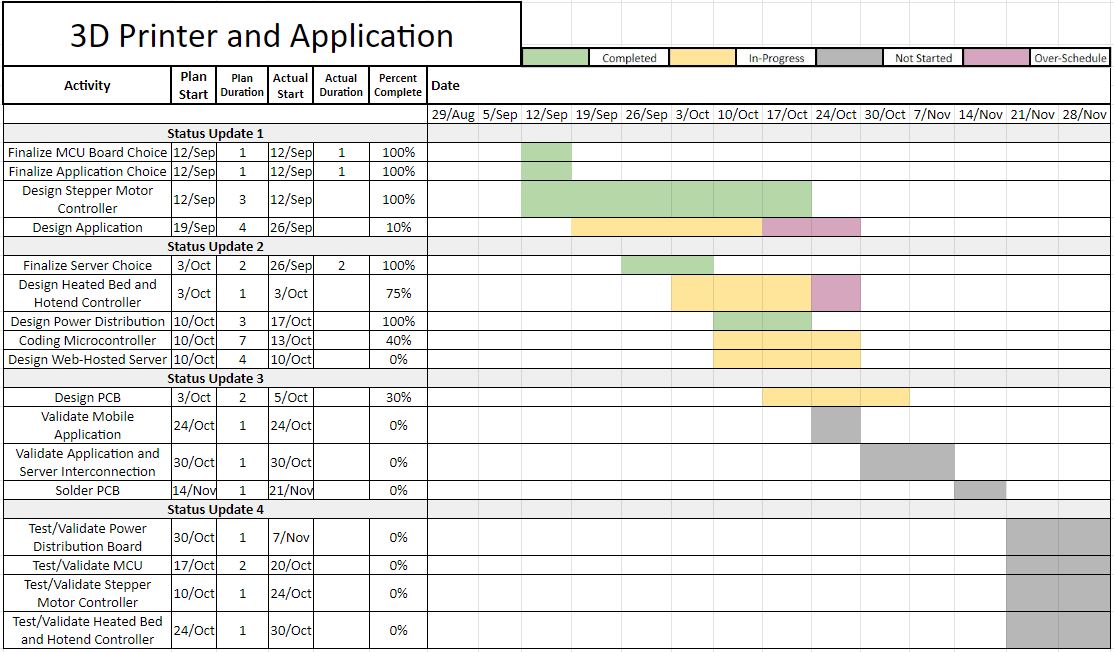
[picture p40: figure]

## Validation Plan

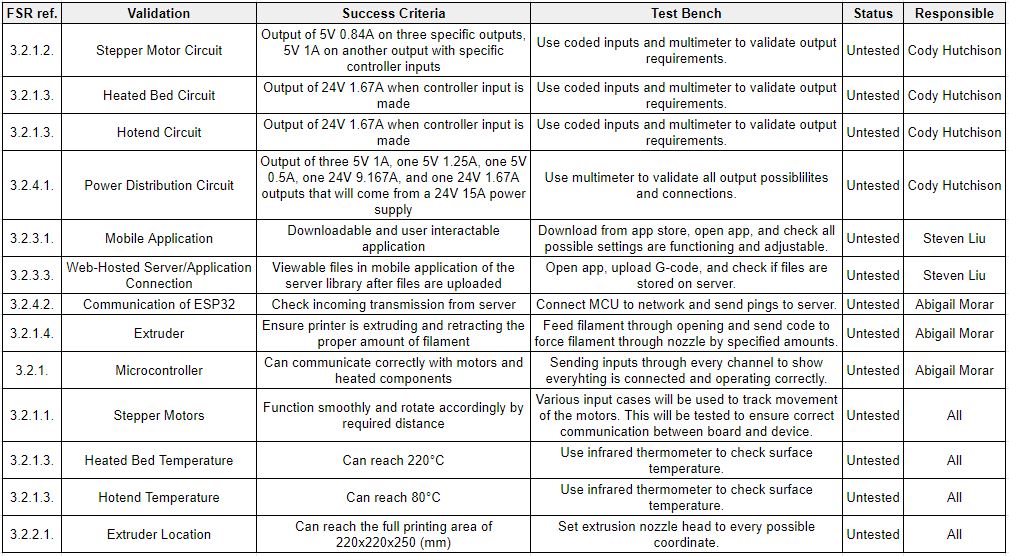
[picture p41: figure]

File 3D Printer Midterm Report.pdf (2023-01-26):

# 3D Printer and Application Interface

# Cody Hutchison Steven Liu Abigail Morar

# MIDTERM REPORT

### Table of Contents

Table of Contents | 2
Concept of Operations | 3
Functional System Requirements | 14
Interface Control Documents | 26
Schedule and Validation | 35

# 3D Printer and Application Interface

# Cody Hutchison Steven Liu Abigail Morar

# CONCEPT OF OPERATIONS

### REVISION – 0.1 14 September 2022

Concept of Operations | Revision 0.1
3D Printer and Application

### CONCEPT OF OPERATIONS

### FOR

## 3D Printer and Application Interface

TEAM 21

APPROVED BY:

_____________________________
Cody Hutchison | Date

_____________________________
Prof. Lusher | Date

_____________________________
Dalton Cyr | Date

Concept of Operations | Revision 0.1

### Change Record

Rev . | Date | Originator | Approvals | Description
0.0 | 9/14/2022 | Dalton Cyr | Cody Hutchison | Draft Release
0.1 | 9/28/2022 | Dalton Cyr | Cody Hutchison | Revision 1

Concept of Operations | Revision 0.1

### Table of Contents

Table of Contents | 6
List of Tables | 7
1. Executive Summary | 8
2. Introduction | 9
2.1. | Background | 9
2.2. | Overview | 9
2.3. | Referenced Documents and Standards | 10
3. Operating Concept | 10
3.1. | Scope | 10
3.2. | Operational Description and Constraints | 10
3.3. | System Description | 11
3.4. | Modes of Operations | 11
3.5. | Users | 11
3.6. | Support | 12
4. | Scenario(s) | 12
4.1. | Parts Rush | 12
4.2. | 3D Printing Business | 12
4.3. | Work Prototype | 12
4.4. | Hobby Printing | 12
5. Analysis | 12
5.1. | Summary of Proposed Improvements | 12
5.2. | Disadvantages and Limitations | 12
5.3. | Alternatives | 12
5.4. | Impact | 13

Concept of Operations | Revision 0.1

### List of Tables

Figure 1. 3D Printer Block Diagram | 9

Concept of Operations | Revision 0.1

## 1. Executive Summary

Common 3D printers require local, in-person interaction to start/stop, format settings, or even insert memory devices to upload files. The sponsor for this project, Dalton Cyr, desires a 3D printer capable of printing files with the portability and ease of using a mobile device from any location. With a thoroughly designed phone application and Wi-Fi capability, this 3D printer will have similar features to other standard 3D printers and can also be controlled from any location with internet access. To print, while away from the 3D printer, it must have a server, and to preserve security, the 3D printer will access a web server provided by Amazon Web Services which has a reputation for customer security and satisfaction. This project will highlight the pleasing and straightforward user experience of printing 3D designs with the speed and quality of other printers through a mobile phone application.

Concept of Operations | Revision 0.1

## 2. Introduction

This document will review the concepts of operation for a 3D printer and its application interface. While many 3D printers require users to handle their operation in person, this 3D printer will solve this issue with a mobile phone application allowing the user to print from their current location. To achieve this task, the project will be broken down, researched, and executed in several subsystems: power supply, microcontroller unit, dedicated web server, and mobile phone application.

### 2.1. Background

The combination of a mobile phone application and the dedicated web server will not only provide ease of use, away from the 3D printer but will also act as a simple form of security and solution for transferring large print files. Using the mobile phone application will minimize the need for a user interface on the printer. The only printer control will be the main power switch placing the printer in a standby state. Physical interactions with the 3D printer consist of the initial setup and powering on, adding PLA rolls to the printer, and removing completed prints.

### 2.2. Overview

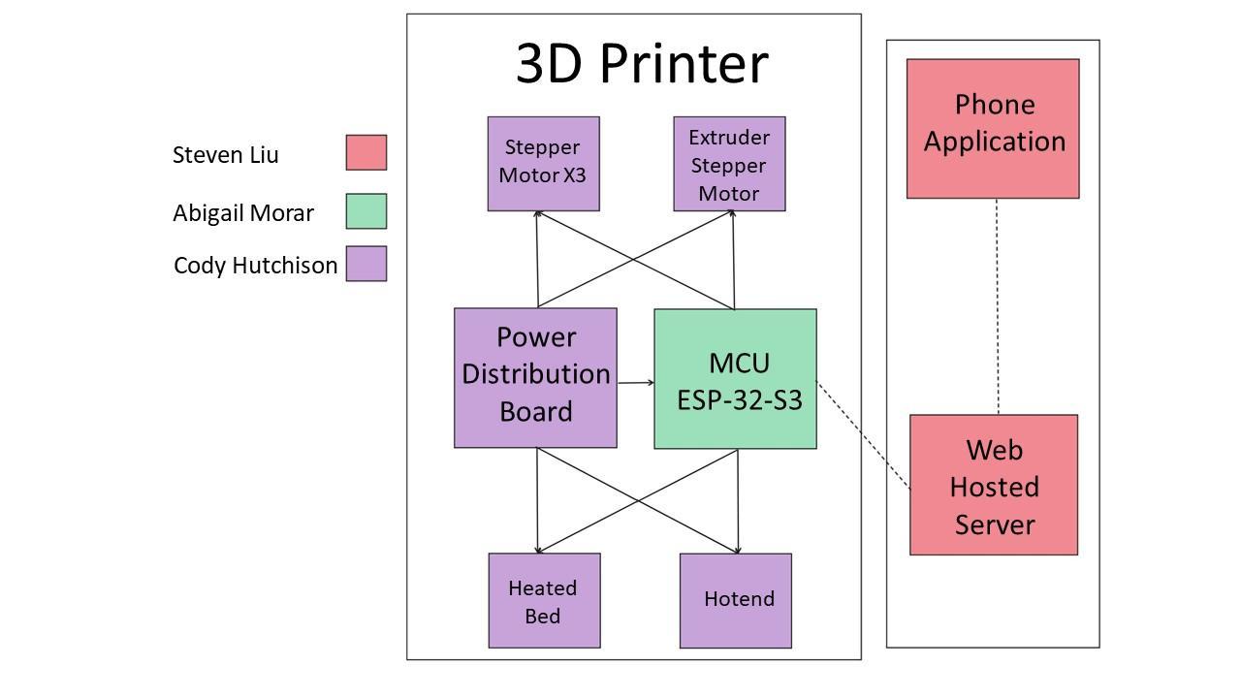
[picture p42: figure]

Figure 1. 3D Printer Block Diagram

This 3D printer will be designed to work exclusively through a mobile phone application. The application will receive commands and files and send them to the web-based server setup for the printer. Once uploaded, the server will store the files in the cloud and pass on commands to the motherboard in the 3D printer, if any are received. The motherboard will

Concept of Operations | Revision 0.1

then read the codes in order of the most recent upload and begin heating the heated bed and hot head. Once the hot head and heated bed are at the required temperature set by the user, the motherboard will start reading the G-code from the server and initiate printing. The motherboard will also send a code to the server that will be forwarded to the application to start the timer. Another transmitted command would be to cancel/end the print in a situation where there is an issue with the print job, an issue with the design and the person does not want to waste PLA, or the user realized there would not be enough filament to complete the job. Once printing is finished, the printer will send a complete command to the server that will be forwarded to the application to notify the individual that the print is done and the timer will be stopped. Power will be distributed to the motherboard, the stepper motors, the hot head, the heated bed, and the extruder for operation and communication between subsystems.

### 2.3. Referenced Documents and Standards

- IEEE Wi-Fi Std 802.11-2020
- IEEE Standard for Safety Levels with Respect to Human Exposure to Electric, Magnetic, and Electromagnetic Fields, 0 Hz to 300 GHz, ANSI C95.1-2019
- Android App Development, “Core App Quality” https://developer.android.com/docs/quality-guidelines/core-app-quality

## 3. Operating Concept

### 3.1. Scope

The goal is to develop a 3D printer that is controlled by a phone application that stores the G-code files on an internet server and allows the printing of the G-code files from anywhere that has internet access.

### 3.2. Operational Description and Constraints

This 3D printer system requires internet access from both the 3D printer and mobile device. Before using the 3D printer, the microcontroller unit will require an initial connection to the web-hosted server and local network at its location with its main power switch on standby. The user will send G-code files and printer commands from the mobile phone application to the server. On the printer side, the microcontroller will send pull requests in intervals receiving packets of the files/commands to control the 3D printer while also sending push requests of collected data to the server. This data is displayed through the mobile application allowing the user to monitor the 3D printer’s progress. The 3D printer design must meet the following criteria:

- Operate within 10-15% speed of the initial hardware and software used for the Ender 3 3D printer
- Print area of 220mm x 220mm x 250mm
- Print height of 0.2 mm per layer
- Use 1.75mm PLA for print material
- The heated bed must reach a maximum temperature of 80℃
- The hot head must reach a maximum temperature of 220 ℃

Concept of Operations | Revision 0.1

The printer will have an input of 120V 60Hz AC power that will be converted to 24V 15A. The system will use an ESP32 microcontroller to communicate with the host server and provide commands to the motherboard. The interface for the 3D printer will be through an android mobile application with the host server designed through Amazon Web Services.

### 3.3. System Description

There are three main subsystems for the 3D printer and mobile phone application. The first subsystem is the interface consisting of the mobile phone application and the web server. The mobile phone application will take G-code files and upload them to a web server and allow the initiation and shutdown of the 3D printer. The application will also handle initializing specific printing specifications desired by the user such as heated bed/hot head temperatures and stepper motor adjustments. Other features of the application are keeping track of print progress, the amount of material used, and housing a library of prints sent from the phone. The web host server will act as an intermediary for file transfer and controls between the phone application and the 3D printer while also housing previous 3D print files.
The second subsystem is the microcontroller for the 3D printer. While in standby mode, the microcontroller will send requests in specified intervals to take in commands from the cloud server and send them to the motherboard. Such commands may include the starting/stopping of printing, the control over fan speed, the location of the hot head, the amount of extruded material, the retraction of filament, and the temperature of the heated components. The motherboard will process and distribute these commands whether in standby or active printing. The movement of the stepper motors will be communicated to the stepper motor control board, and adjusting the temperature of the heated bed and hot head will be communicated to their boards, respectively. The microcontroller will also collect information to be sent back to the phone application allowing the user to monitor the printing progress and selected print settings.
The third subsystem will be the motor controller boards, temperature controlling boards, and a power distribution board. The motor controller boards will take commands from the microcontroller and send power to the stepper motors by use of dual H-bridges. The temperature control board will also send power to the heated bed and hot head by the use of MOSFETs and signals from the microcontroller. The power distribution board will take the 24V 15A, split it up, and send 5V 1.5A to all 4 stepper motors; 5V 0.5A to the microcontroller, 24V 9.167A to the heated bed, and 24V 1.67A to the hot head.

### 3.4. Modes of Operations

There is a single planned mode of operation for the 3D printer electronic system. That operation is to control the 3D printer through a mobile phone application that requires only a main power switch on the printer to stop all external power.

### 3.5. Users

This 3D printing system is aimed toward hobbyist 3D printers. The setup requires basic knowledge to connect the printer's built-in microcontroller to the web server and local network by following the instructions in the manual. After the server's setup is complete, anyone with proper G-code files and an internet connection can use the printer.

Concept of Operations | Revision 0.1

### 3.6. Support

The manual will provide assembly instructions for the 3D printer as well as instructions to set up the connection to the web server and local network. The manual will also display the mobile application name and link to download it. The app will provide a walkthrough of all its features along with how to send print files, adjust heating components or extruder positioning, and start or stop a print design.

## 4. Scenario(s)

### 4.1. Parts Rush

- Parts rush required due to competition schedule and broken parts so prints may be initiated while traveling from a competition.

### 4.2. 3D Printing Business

- Need to start a print order while out of the office to meet customer deadlines.

### 4.3. Work Prototyping

- Modifications are required on a prototype 3D print that cannot be finished at work. Allows employees to finish adjustments and initiate printing from home.

### 4.4. Hobby Printing

- Allows hobbyists to print from any location as long as there is internet connection.

## 5. Analysis

### 5.1. Summary of Proposed Improvements

Improvements include user-friendly setup, ease of feature adjustments, print progress notifications, the ability to start and stop jobs remotely, virtually infinite file storage, faster auto-home command, and convenient communication between devices.

### 5.2. Disadvantages and Limitations

Feeding issues could be a major disadvantage to this system. This would be caused by a clog in the extruder or the 3D printer running out of filament. The limitation of having only a phone application to communicate with the 3D printer would prove to be a problem if the local network is ever down since the device can only print files when connected over the internet.

### 5.3. Alternatives

One alternative is that the printer could be controlled through Bluetooth instead of a network connection to the server. A drawback to that would be the need for users to stay within range of the printer to control and operate it.

### 5.4. Impact

Possible impacts:

Concept of Operations | Revision 0.1
1. The capability to 3D print from anywhere, allows people to be more social and not be confined to their homes to print an item.
2. With the freedom of not having to constantly monitor the printer, the individual can now volunteer to clean up around their neighborhood, town, or city.
3. By making the 3D printer user-friendly, it allows people who are not technically inclined to a platform to perform 3D printing.
4. An ethical issue would be leaving the printer to run unattended with the 80℃ heated bed and a 200℃ hot head. A fire could occur if a flammable item fell onto the hot head or heated bed. Without supervision, these heated components could cause dangerous outcomes such as a major injury to another person or pet.

Concept of Operations | Revision 0.1

# 3D Printer and Application Interface

# Cody Hutchison Steven Liu Abigail Morar

# FUNCTIONAL SYSTEM REQUIREMENTS

### REVISION – 0.0 3 October 2022

Functional System Requirements Revision 0.0

### FUNCTIONAL SYSTEM REQUIREMENTS

### FOR

## 3D Printer and Application

TEAM 21

_____________________________
Author | Date

APPROVED BY:

_____________________________
Cody Hutchison | Date

_____________________________
John Lusher, P.E. | Date

_____________________________
Dalton Cyr | Date

Functional System Requirements Revision 0.0

### Change Record

Rev . | Date | Originator | Approvals | Description
0.0 | 10/3/2022 | Dalton Cyr | Cody Hutchison | Draft Release

Functional System Requirements Revision 0.0

### Table of Contents

Table of Contents | 17
List of Tables | 18
List of Figures | 18
1. 3119
1.1. 89
1.2. 920
2. 920
2.1. 1020
2.2. 1020
2.3. 1021
3. 1021
3.1. 1121
3.2. 1122
3.2.1. 1222
3.2.2. 1222
3.2.3. Software Characteristics | 23
3.2.4. 1223
3.2.5. 1223
4. 1224
Appendix A: Acronyms and Abbreviations | 25
Appendix B: Definition of Terms | 25
Appendix C: Interface Control Documents | 25

Functional System Requirements Revision 0.0

### List of Tables

Table 1. Subsystems and Responsibilities | 20
Table 2. Applicable Documents | 20
Table 3. Reference Documents | 20

### List of Figures

Figure 1. Ender 3 3D printer | 19
Figure 2. Block Diagram of System | 21

Functional System Requirements Revision 0.0

## 1. Introduction

### 1.1. Purpose and Scope

The 3D Printer will provide an efficient solution to users who desire to 3D print remotely. This project shall incorporate the use of a mobile application, AWS cloud computing service, and onboard internet capabilities along with common 3D printing hardware to achieve this goal. The 3D printer shall retain the same options as the printer's original hardware and software offered. The project will be divided into several subsystems listed below in Table 1.

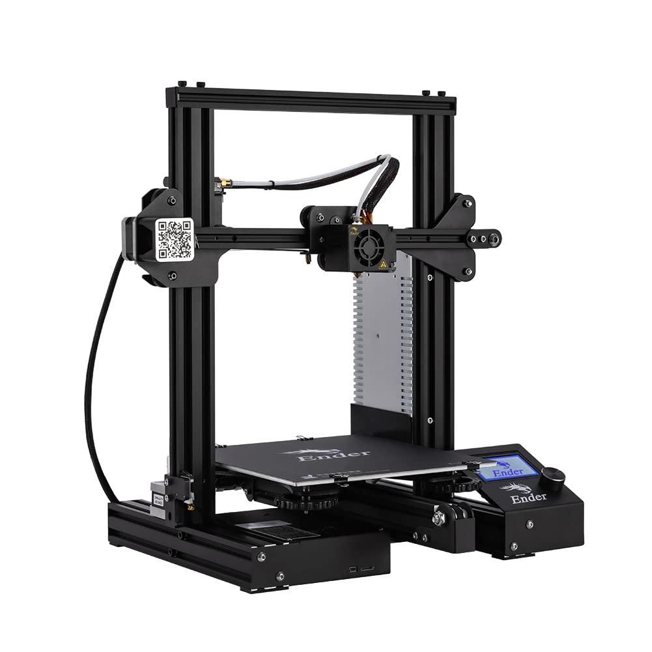
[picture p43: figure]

Figure 1. Ender 3 3D printer

Functional System Requirements Revision 0.0

### 1.2. Responsibility and Change Authority

The team leader, Cody Hutchison, will ensure all project requirements will be met and that the team will keep to the planned schedule. All subsystems and respective responsibilities are listed below in Table 1. Any and all changes must be approved by the team leader and Sponsor, Dalton Cyr. Cody Hutchison is responsible for the stepper motor controller, the heating elements of the hot head and hot bed, and the correct power distribution to all the required hardware components. Steven Liu is in charge of the development of the 3D printer application and making sure it connects to the web-hosted server. He is also responsible for the development of the server which will communicate with the MCU. Abigail Morar is responsible for the microcontroller and ensuring that it is sending and receiving signals appropriately, as well as communicating between each component and subsystem effectively.

Subsystem | Responsibility
Power Distribution | Cody Hutchison
Onboard Hardware | Cody Hutchison
Onboard Software | Abigail Morar
AWS Server | Steven Liu
Mobile Application | Steven Liu
Table 1. Subsystems and Responsibilities

## 2. Applicable and Reference Documents

### 2.1. Applicable Documents

Document Number | Revision/Release Date | Document Title
Ender 3 Printer Manual | | Ender 3 Printer Manual
ESP32-S3 Series | V1.3 | ESP32-S3 Series Datasheet
802.11-2020 | 08 October 2021 | IEEE Standard of for Information Technology
Table 2. Applicable Documents

### 2.2. Reference Documents

Document Number | Revision/Release Date | Document Title
N/A | N/A | Android App Development

Table 3. Reference Documents

### 2.3. Order of Precedence

In the event of a conflict between the text of this specification and an applicable document cited herein, the text of this specification takes precedence without any exceptions.

Functional System Requirements Revision 0.0

All specifications, standards, exhibits, drawings, or other documents that are invoked as “applicable” in this specification are incorporated as cited. All documents that are referred to within an applicable report are considered to be for guidance and information only, except ICDs that have their relevant documents considered to be incorporated as cited.

## 3. Requirements

### 3.1. System Definition

The project is to design a control system and application that allows the printer to be operated by an application from anywhere there is internet access.

Figure 2. Block Diagram of System

The three main subsystems are the MCU programming, the android application and web server, and finally the control and power distribution board. The reason for changing the 3D printer design is to convert it from being manually operated through the application only. The original hardware was all combined into two boards which is the reason for building all the different boards.

Functional System Requirements Revision 0.0

### 3.2. Characteristics

### 3.2.1. Functional / Performance Requirements

### 3.2.1.1. Print Time

Constraining the print time within 10-15% of the time it takes to print with the original hardware and software.

Rationale: This is a requirement specified by the customer to meet the capabilities set by
the old software.

### 3.2.1.2. Axis Speed

Increase the Z-axis speed so that it is closer to the speed of the X and Y-axis.

Rationale: By increasing the Z-axis speed allows the movement of the hotend and home return.

### 3.2.1.3. Temperature Control

The heated bed needs to be controllable from 0-80℃ and the hot end needs to be controllable from 0-220℃.

Rationale: This is a requirement specified by the customer to have the heated components
be heated enough for PLA filament to be properly used. These temperature ranges allow adjustability for different brands of PLA.

### 3.2.1.4. Printing Layer Height

Each layer will have a height of 0.2mm.

Rationale: This is a requirement specified by the customer since this is the common printing height of the filament.

### 3.2.2. Physical Characteristics

### 3.2.2.1. Print Area

The printing area will be 220mm x 220mm x 250mm.

Rationale: This is a requirement specified by the customer due to the printing area of the original 3D printer base/frame being used.

### 3.2.2.2. Printing Material

The printing material needs to be 1.75mm PLA.

Rationale: This is a requirement specified by the customer since this printing material is common and affordable.

Functional System Requirements Revision 0.0

### 3.2.3. Software Characteristics

### 3.2.3.1. Mobile Application

The mobile application shall be developed for Android devices.

Rationale: The application is done for Android devices due to an accessible developmental environment and available tools.

### 3.2.3.2. Mobile Application Software

The mobile application software shall be developed using the Kotlin programming language.

Rationale: The Kotlin language is chosen due to its compatibility with android application development.

### 3.2.3.3. Web-Hosted Server

The intermediary server shall be developed using Amazon Web Services.

Rationale: AWS is chosen for its reputable performance, quality and security. AWS has a wide variety of integrable services that meet the needs of the customer.

### 3.2.4. Electrical Characteristics

### 3.2.4.1. System Power

### 3.2.4.1.1 Power Consumption

The total power consumption shall not exceed 360 W.

Rationale: The maximum amount of power consumption was below 360 Watts and the maximum output of our power supply is 360 Watts.

### 3.2.4.2. Outputs

### 3.2.4.2.1 Data Output

The 3D Printing System shall include an interface to view the printing progress.

Rationale: The 3D printer sends progress data back to the user through the server and mobile application.

### 3.2.5. Failure Propagation

The 3D Printing System shall not allow failure propagation beyond the server.

### 3.2.5.1. Failure Detection

The 3D Printing System shall have a software subsystem in the server to check if the G-code files to be printed will fit within the 3D printing size constraints and if the heated elements are within proper printing temperatures.

Rationale: This is a requirement to avoid oversized prints due to large print designs and
poor adhesion of print layers due to inadequate extrusion and hot bed temperatures.

Functional System Requirements Revision 0.0

### 3.2.5.2. Failure Warning

The 3D Printing System will record how much filament has ever been used to notify the user of potential print failure when filament is estimated to run out.

Rationale: Users will be able to account for and resolve problems when they are planning
to print remotely.

## 4. Support Requirements

The 3D printer and application will require an internet connection and access to 120VAC 60Hz power. The web-hosted server will also require an initial setup through the amazon web-hosted server website. The 3D printer will require some assembly. If taken to a new location where the local network is changed, a new connection setup with the web-hosted server will have to take place. The phone application will need to be downloaded onto an android device with Wi-Fi/internet connection capability.

Functional System Requirements Revision 0.0

## - Appendix A: Acronyms and Abbreviations

3D | 3 Dimensional
A | Amperage
AWS | Amazon Web Services
C | Celsius
G-code | Geometric Code
GHz | Gigahertz
Hz | Hertz
MHz | Megahertz
ICD | Interface Control Document
IEEE | Institute of Electrical and Electronic Engineers
MCU | Microcontroller Unit
mm | Millimeter
oz | Ounce
PCB | Printed Circuit Board
PLA | Polylactic Acid
V | Voltage
VAC | Volts Alternating Current
W | Watts

## - Appendix B: Definition of Terms

## Appendix C: Interface Control Documents

Functional System Requirements Revision 0.0

# 3D Printer and Application Interface

# Cody Hutchison Steven Liu Abigail Morar

# INTERFACE CONTROL DOCUMENT

### REVISION – 0.0 3 October 2022

Interface Control Document | Revision - 0.0

### INTERFACE CONTROL DOCUMENT

### FOR

## 3D Printer and Application

TEAM 21

_____________________________
Author | Date

APPROVED BY:

_____________________________
Cody Hutchison | Date

_____________________________
John Lusher II, P.E. | Date

_____________________________
Dalton Cyr | Date

Interface Control Document | Revision - 0.0

### Change Record

Rev . | Date | Originator | Approvals | Description
0.0 | 10/3/2022 | Dalton Cyr | Cody Hutchison | Draft Release

Interface Control Document | Revision - 0.0

### Table of Contents

Table of Contents | 29
List of Tables | 30
List of Figures | 30
1. Overview | 31
2. References and Definitions | 31
2.1. | References | 31
2.2. | Definitions | 31
3. Physical Interface | 31
3.1. 1131
3.2. | Dimensions | 32
4. 1232
4.1. | Primary Input Power | 33
4.1.1. Power Supply | 33
4.1.2. Power Distribution | 33
4.2. | Voltage and Current Levels | 33
4.3. | Signal Interface | 33
4.3.1. ESP32-S3 Signal Interface | 33
5. Communication / Device Interface Protocol | 34
5.1. | Wireless Communication (Wi-Fi) | 34

Interface Control Document | Revision - 0.0

### List of Tables

Table 1. PCB Dimensions | 31
Table 2. PCB Weights | 32
Table 3. Component power usage | 33

### List of Figures

- Figure 1. Electrical Interface Diagram | 32
- Figure 2. ESP32-S3 Layout | 34

Interface Control Document | Revision - 0.0

## 1. Overview

The interface control document details how the microcontroller is interfacing with all the other control boards, the web-hosted server, and the application.

## 2. References and Definitions

### 2.1. References

Refer to section 2.2 of the Functional System Requirements document.

### 2.2. Definitions

Refer to Appendix A of the Functional System Requirements document.

## 3. Physical Interface

### 3.1. Weight

Component | Weight (oz) | Number of Items | Total Weight
ESP32-S3 | TBD | 1 | TBD
Stepper Motor Control Board | TBD | 4 | TBD
Heated Bed Control Board | TBD | 1 | TBD
Hotend Control Board | TBD | 1 | TBD
Power Distribution Board | TBD | 1 | TBD

Table 1. PCB Dimension

Interface Control Document | Revision - 0.0

### 3.2. Dimensions

Component | Length (mm) | Width (mm)
ESP32-S3 | 62.74 | 25.4
Stepper Motor Control Board | TBD | TBD
Heated Bed Control Board | TBD | TBD
Hotend Control Board | TBD | TBD
Power Distribution Board | TBD | TBD
Table 2. PCB Weights

## 4. Electrical Interface

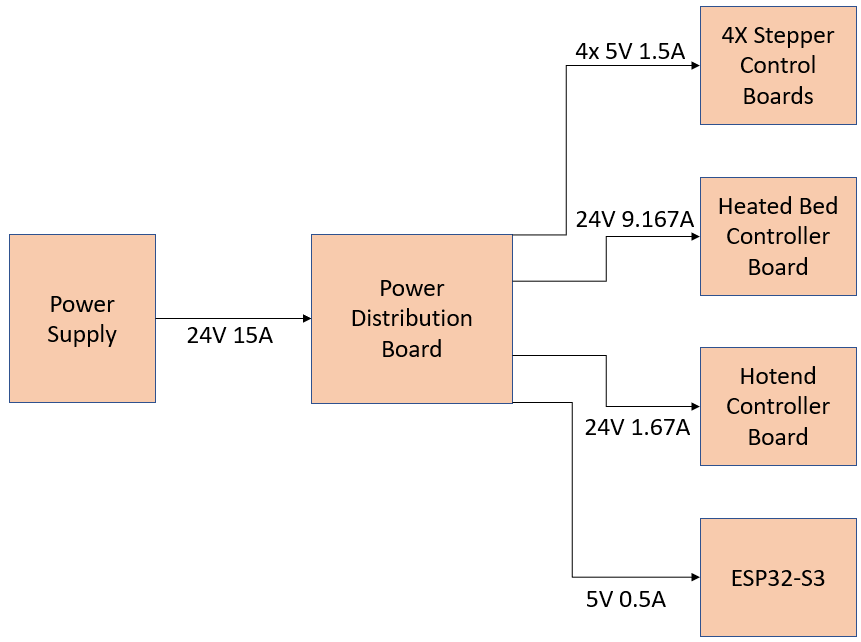
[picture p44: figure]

Figure 1. Electrical Interface Diagram

Interface Control Document | Revision - 0.0

### 4.1. Primary Input Power

### 4.1.1. Power Supply

The power supply coming in will be 24V 15A and is the original power supply that the 3D printer had.

### 4.1.2. Power Distribution

The power distribution board will take the 24V 15A and distribute the power required to each board.

### 4.2. Voltage and Current Levels

Components | Voltage (V) | Current (A) | Power (W)
ESP32-S3 | 5 | 0.5 | 2.5
Stepper Motor Control Board | 5 | 1.5 | 7.5
Heated Bed Control Board | 24 | 9.167 | 220
Hotend Control Board | 24 | 1.67 | 40
Power Distribution Board | 24 | 15 | 360

Table 3. Component power usage

### 4.3. Signal Interfaces

### 4.3.1. ESP32-S3 Signal Interface

The ESP32-S3 will be controlled by a built-in 802.11 b/g/n 2.4 GHz Wi-Fi + Bluetooth module. It will be connected to the server and motherboard.

Interface Control Document | Revision - 0.0

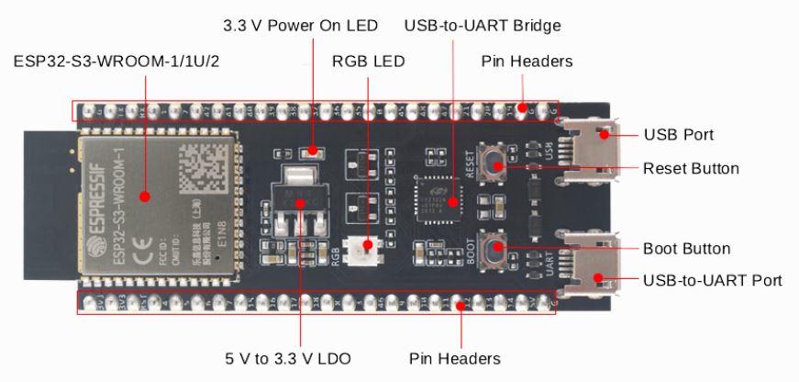
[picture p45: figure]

Figure 2. ESP32-S3 Layout

## 5. Communications / Device Interface Protocols

### 5.1. Wireless Communications (Wi-Fi)

The ESP32-S3 has a Wi-Fi module built into the board that follows the IEEE 802.11 b/g/n standard protocol. This will allow the microcontroller to be controlled by the application through the Wi-Fi and web-hosted server.

Interface Control Document | Revision - 0.0

# 3D Printer and Application Interface

# Cody Hutchison Steven Liu Abigail Morar

# SCHEDULE AND VALIDATION PLAN

### REVISION – 0.0 3 October 2022

Interface Control Document | Revision - 0.0

### SCHEDULE AND VALIDATION PLAN

### FOR

## 3D Printer and Application

TEAM 21

_____________________________
Author | Date

APPROVED BY:

_____________________________
Cody Hutchison | Date

_____________________________
John Lusher, P.E. | Date

_____________________________
Dalton Cyr | Date

Interface Control Document | Revision - 0.0

### Change Record

Rev . | Date | Originator | Approvals | Description
0.0 | 10/3/2022 | Dalton Cyr | Cody Hutchison | Draft Release

Interface Control Document | Revision - 0.0

### Table of Contents

Table of Contents | 38
List of Tables | 39
1. Execution Plan | 40
2. Validation Plan | 41

Interface Control Document | Revision - 0.0
| List of Tables
Table 1. Gantt Chart | 40
Table 2. Validation Table | 41

Interface Control Document | Revision - 0.0

## 1. Execution Plan

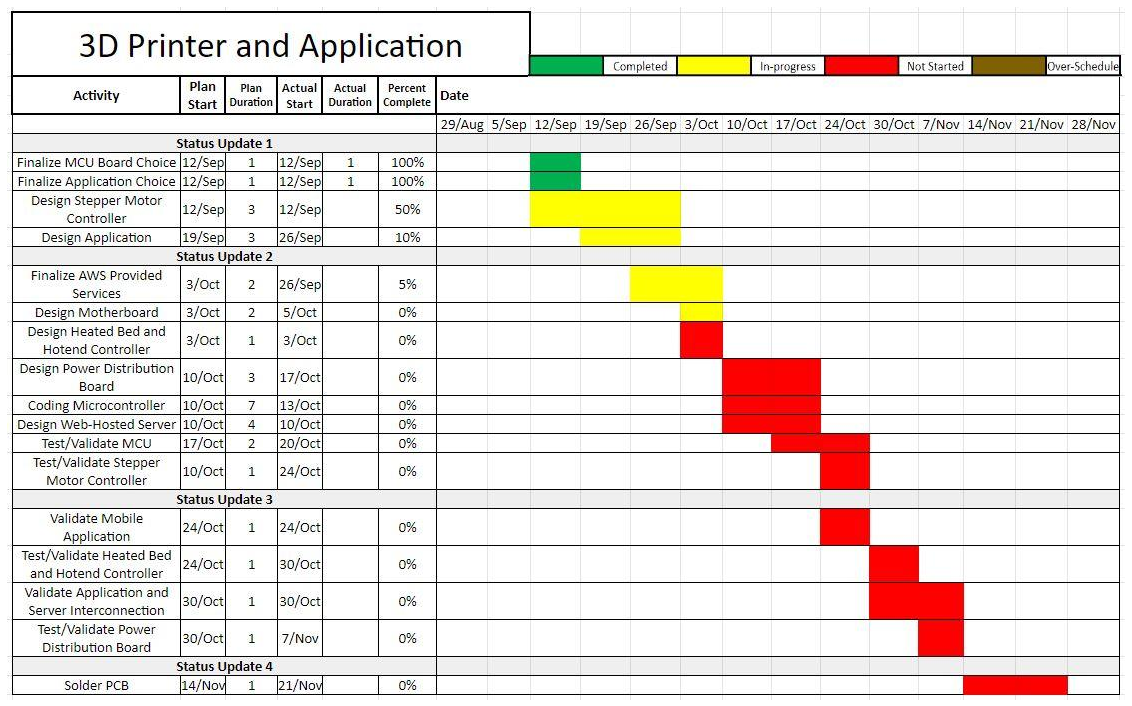
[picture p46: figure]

Table 1. Gantt Chart

Interface Control Document | Revision - 0.0

## 2. Validation Plan

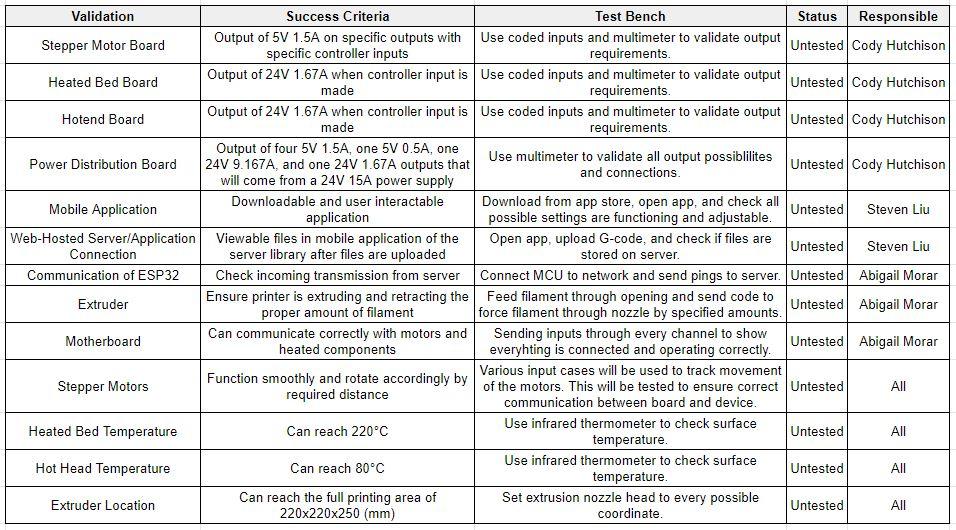
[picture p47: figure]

Table 2. Validation Table

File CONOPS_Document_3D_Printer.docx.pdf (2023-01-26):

# 3D Printer and Application Interface

# Cody Hutchison Steven Liu Abigail Morar

## CONCEPT OF OPERATIONS

### REVISION – 0.0 14 September 2022

CONCEPT OF OPERATIONS

FOR

## 3D Printer and Application Interface

TEAM 21

APPROVED BY:

_____________________________
Cody Hutchison | Date

_____________________________
Prof. Lusher | Date

_____________________________
Dalton Cyr | Date

Concept of Operations | Revision - 0.0
3D Printer and Application Interface your

### Change Record

Rev . | Date | Originator | Approvals | Description
0.0 | 9/14/2022 | Dalton Cyr | Cody Hutchison | Draft Release

### Table of Contents

Table of Contents | 3
List of Figures | 4
1. Executive Summary | 5
2. Introduction | 6
2.1. Background | 6
2.2. Overview | 6
2.3. Referenced Documents and Standards | 7
3. Operating Concept | 8
3.1. Scope | 8
3.2. Operational Description and Constraints | 8
3.3. System Description | 8
3.4. Modes of Operations | 9
3.5. Users | 9
3.6. Support | 9
4. Scenario(s) | 10
4.1. Parts Rush | 10
4.2. Printing on the Go | 10
4.3. Work Prototyping | 10
4.4. Hobby Printing | 10
4.5. Multidisciplinary Skills | 10
5. Analysis | 11
5.1. Summary of Proposed Improvements | 11
5.2. Disadvantages and Limitations | 11
5.3. Alternatives | 11
5.4. Impact | 11

### List of Tables

### Fig 1: 3D Printer Block Diagram

## 1. Executive Summary

Common 3D printers require local, in-person interaction to start/stop, format settings, or even insert memory devices to upload files. The sponsor for this project, Dalton Cyr, desires a 3D printer capable of printing files with the portability and ease of using a mobile device from any location. With a thoroughly designed phone application and wifi capability, this 3D printer will have similar features to other standard 3D printers and can also be controlled from any location with internet access. To print, while away from the 3D printer, it must have a server, and to preserve security, the 3D printer will access a web server provided by Amazon Web Services which has a reputation for customer security and satisfaction. This project will highlight the pleasing and straightforward user experience of printing 3D designs with the speed and quality of other printers through a mobile phone application.

## 2. Introduction

This document will review the concepts of operation for a 3D printer and its application interface. While many 3D printers require users to handle their operation in person, this 3D printer will solve this issue with a mobile phone application allowing the user to print from their current location. To achieve this task, the project will be broken down, researched, and executed in several subsystems: power supply, microcontroller unit, dedicated web server, and mobile phone application

### 2.1. Background

The combination of a mobile phone application and the dedicated web server will not only provide ease of use, away from the 3D printer but will also act as a simple form of security and solution for transferring large print files. Using the mobile phone application will minimize the need for a user interface on the printer. The only printer control will be the main power switch placing the printer in a standby state. Physical interactions with the 3D printer consist of the initial setup and powering on, adding PLA rolls to the printer, and removing completed prints.

### 2.2. Overview

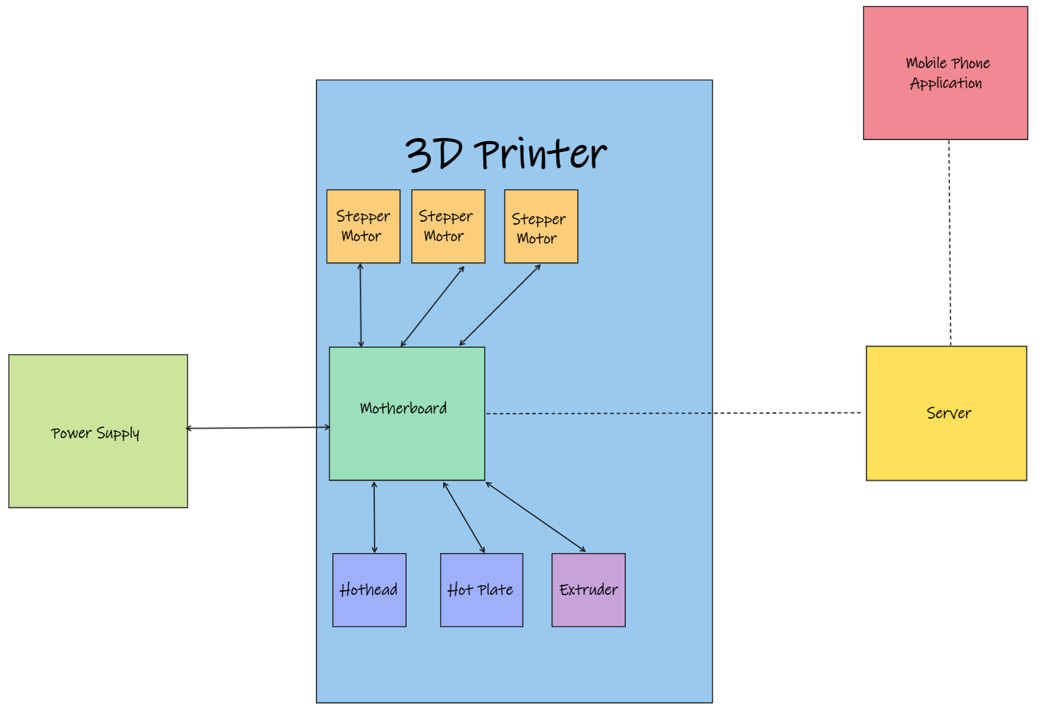
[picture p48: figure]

Fig 1: 3D Printer Block Diagram

This 3D printer will be designed to work exclusively through a mobile phone application. The application will take in commands and files and send them to the web-based server setup for the printer. Once uploaded, the server will store the files and pass on commands to the motherboard in the 3D printer if any are received. The motherboard will then read the codes and in one situation initiate the printing by heating the hot plate and hothead. Once the hothead and heated bed are at temperature, the motherboard will start reading the G-code from the server and initiate printing. The motherboard will also send a code to the server to forward to the application to start the timer. Another command that would be sent would be to cancel/end print in a situation where there is an issue with the print or an issue with the design and the person doesn't want to waste PLA. Once printing is completed the printer will then send a complete command to the server to forward to the application to notify the individual that the print is complete and stop the timer. To operate the 3D printer, a power supply will be built that can power the motherboard, the stepper motors, the hothead, the hot plate, and the extruder.

### 2.3. Referenced Documents and Standards

- IEEE Wi-Fi Std 802.11-2020
- IEEE Standard for Safety Levels with Respect to Human Exposure to Electric, Magnetic, and Electromagnetic Fields, 0 Hz to 300 GHz, ANSI C95.1-2019
- Android App Development, “Core App Quality” https://developer.android.com/docs/quality-guidelines/core-app-quality

## 3. Operating Concept

### 3.1. Scope

The goal is to develop a 3D printer that is controlled by a phone application that stores the G-code files on an internet server and allows the printing of the G-code files from anywhere with internet access.

### 3.2. Operational Description and Constraints

This 3D printer system requires internet access from both the 3D printer and mobile device. Before using the 3D printer, its built-in microcontroller unit requires an initial connection to the web-hosted server and local network at its location with its main power switch on standby. The user will send G-code files and printer commands from the mobile phone application to the server. On the printer side, the microcontroller will send pull requests in intervals receiving packets of the files/commands to control the 3D printer while also sending push requests of collected data to the server. This data is displayed through the mobile application allowing the user to monitor the 3D printer’s progress. The 3D printer design must meet the following criteria:

- Operate within 10-15% speed of the initial hardware and software used for the Ender 3 3D printer
- Print area of 220mm x 220mm x 250mm
- Print height of 0.2 mm per layer
- Use 1.75mm PLA for print material
- The heated bed must reach a maximum temperature of 80℃
- The hothead must reach a maximum temperature of 220 ℃

The printer will have an input of 120V 60Hz AC power that will be converted to 24V 15A. The system will use an esp32 microcontroller to communicate with the host server and provide commands to the motherboard. The interface for the 3D printer will be through an android mobile application with the host server designed through Amazon Web Services.

### 3.3. System Description

There are three main subsystems for the 3D printer and mobile phone application. The first subsystem is the interface consisting of the mobile phone application and the web server. The mobile phone application will take G-code files and upload them to a web server and allow the initiation and shutdown of the 3D printer. The application will also handle initializing specific printing specifications desired by the user such as heated bed/hothead temperatures and stepper motor adjustments. Other features of the application are keeping track of print progress, the amount of material used, and housing a library of prints sent from the phone. The web host server will act as an intermediary for file transfer and controls between the phone application and the 3D printer while also housing previous 3D print files. The second subsystem is the motherboard and microcontrollers for the 3D printer. While in standby mode, the microcontroller will send requests every so often to take in commands from the cloud server and send the commands to the motherboard. Some such commands require printing and the start and stop of printing. The motherboard will process and distribute the commands such as the movement of the stepper motors to the stepper motor control board or regulating the temperature of the hotbed and hothead to meet the specified temperatures. The microcontroller will also collect information to be sent back to the phone application allowing the user to monitor printing progress.
The third subsystem will be the power supply. The power supply will take 120V 60z AC power and convert it into 24Vs capable of supplying 15A worth of current. To power the motherboard, hot plate, hothead, extruder, and all three stepper motors, the power supply will use DC-DC converters to supply each component with its specified voltage. The power supply will also provide overload and overvoltage protection.

### 3.4. Modes of Operations

There is a single planned mode of operation for the 3D printer electronic system. That operation is to control the 3D printer through a mobile phone application that requires only a main power switch on the printer to stop all external power.

### 3.5. Users

This 3D printing system is aimed toward hobbyist 3D printers. The setup requires some basic knowledge to connect the printer's built-in microcontroller to the web server and local network by following the instructions in the manual. After the server's setup is completed, anyone with proper G-code files can use the printer.

### 3.6. Support

The manual will provide assembly instructions for the 3D printer as well as instructions to set up the connection to the web server and local network. The manual will also display the mobile application name and link to download it. The app will provide a walkthrough of all its features along with how to send print files, adjust heating components or motor positioning, and start or stop a print design.

## 4. Scenario(s)

### 4.1. Parts Rush

A man at a drone competition has a build that uses as many 3D parts as possible. After a challenging event, one of the structural components broke. He has a 10-hour drive back home and must have the drone operating within 16 hours of getting there. The necessary part takes 18 hours to print. Luckily, with the mobile phone application and the 3D printer on standby, he only needs to select the part from the saved library of print designs and initiate the printing process. After arriving home the following day, his part will be completed and ready to be installed on the drone in time for the next match.

### 4.2. Printing on the Go

An Etsy store owner’s business is booming and her 3D printer is operating 24/7. She is out running errands when she receives a new order notification for a 3D trinket. She promises same-day shipping on new orders placed before a certain time of day but fears she will not be home in time to start the print and ship it. So she opens the application on her phone and uploads the new order’s file to start printing. When she arrives home, the print will be completed and she can keep her shop’s positive reputation.

### 4.3. Work Prototyping

A woman brings in a prototype of a design she 3D printed last night for her boss to examine. After seeing it, the boss decides to make some adjustments and tells her that he wants to see the updated version of it by tomorrow. She drafts the new piece in SolidWorks, slices it, and uploads the G-code to her phone. From the office, she sends the G-code file and print command through the dedicated web server. By the time she arrives home, the job is finished and ready to be inspected, allowing enough time for a reprint if necessary.

### 4.4. Hobby Printing

A hobbyist’s mind is constantly running and coming up with new ideas. Whether in another room of the house, at a neighbor's, or commuting on a bus, they are always drawing up designs for inventions to improve their life. No matter where they are, they can quickly bring their designs to life by drafting them, sending files through the app, and starting the print job remotely so that they can maintain productivity in their bustling life.

### 4.5. Multidisciplinary Skills

A man with a passion for woodworking, metalworking, 3D printing, and electrical engineering is often busy crafting new designs. He always finds a way to incorporate all of his interests together into one project. Whether he is soldering something in the garage or working with a bandsaw, he can now easily use the 3D printing app to check what is printing and how much longer till the job is complete. Doing so is less intrusive, saves time, and lets him focus on the tasks at hand.

## 5. Analysis

### 5.1. Summary of Proposed Improvements

Improvements include user-friendly setup, ease of feature adjustments, print progress notifications, the ability to start and stop jobs remotely, virtually infinite file storage, and convenient communication between devices.

### 5.2. Disadvantages and Limitations

A major disadvantage would be if there is a feeding issue with the 3D printer such as running out of filament. The limitation of having only a phone application to communicate with the 3D printer would prove to be a problem if wifi is down since the device can only print files when connected over the internet.

### 5.3. Alternatives

One alternative is that the printer could be controlled through Bluetooth instead of a network connection to the server. A drawback to that would be the need for users to stay within range of the printer to control and operate it.

### 5.4. Impact

Possible impacts:

1. The capability to 3D print from anywhere, allows people to be more social and not be confined to their homes to print an item.
2. With the freedom of not having to constantly monitor the printer, the individual can now volunteer to clean up around their neighborhood, town, or city.
3. By making the 3D printer user-friendly, it allows people who are not technically inclined to a platform to perform 3D printing.
4. An ethical issue would be leaving the printer to run unattended with the 80℃ hot plate and a 200℃ hothead. This could lead to a fire if a short occurs, it is knocked over, or even if something falls on the 3D printer. Without supervision, these heated components could cause dangerous outcomes such as a major injury to another person or pet.

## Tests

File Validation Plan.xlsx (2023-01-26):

FSR ref. | Validation | Success Criteria | Test Bench | Status | Responsible
3.2.1.2. | Stepper Motor Circuit | Output of 5V 0.84A on three specific outputs, 5V 1A on another output with specific controller inputs | Use Function Generator, DC power generator, controller board, and multimeter to validate output requirements. | Tested Not Validated | Cody Hutchison
3.2.1.3. | Heated Bed Circuit | Output of 24V 9.167A when controller input is made | Use Function Generator, DC power generator, controller board, and multimeter to validate output requirements. | Tested | Cody Hutchison
3.2.1.3. | Hotend Circuit | Output of 24V 1.67A when controller input is made | Use Function Generator, DC power generator, controller board, and multimeter to validate output requirements. | Tested | Cody Hutchison
3.2.1.3. | Fan 1 and 2 Circuit | Output of 24V 100mA when controller input is made | Use Function Generator, DC power generator, controller board, and multimeter to validate output requirements. | Tested | Cody Hutchison
3.2.4.1. | Power Distribution Circuit | Ensure DC-DC convertor takes 24V input and outputs 5V | Use multimeter to validate all output possiblilites and connections. | Tested | Cody Hutchison
3.2.3.1. | Full Printer Control Features | User choosen printer formatting, file selection, and print initiation | Input printer formatting, select print file, select print initiation and check server for verification | Tested | Steven Liu
3.2.3.2. | Application File Chooser | Application succussfully selects device files | Perform file upload to server and check firebase storage for verification | Tested | Steven Liu
3.2.3.3. | Interactive Library View | Library displays print files that users can select | Attempt print initiation and check server and home tab for verfication | Tested | Steven Liu
3.2.3.4. | Server Storage | Stores print files | Upload print file and retrieve download url | Tested | Steven Liu
3.2.3.5. | Server Realtime Database | Saves print data and accessible print data | attempt printer formatting change and file upload, verify data in server and library tab | Tested | Steven Liu
3.2.3.6. | Application and Server Connection | Successful communication between application and server | Attempt all application printer features and verify communication to server | Tested | Steven Liu
3.2.4.2. | Communication of ESP32 | Check incoming transmission from server | Connect MCU to network and send pings to server. | Tested | Abigail Morar
3.2.1.4. | Extruder | Ensure printer is extruding and retracting the proper amount of filament | Feed filament through opening and send code to force filament through nozzle by specified amounts. | Untested | Abigail Morar
3.2.1. | Microcontroller | Can communicate correctly with motors and heated components | Sending inputs through every channel to show everything is connected and operating correctly. | Untested | Abigail Morar
3.2.1.1. | Stepper Motors | Function smoothly and rotate accordingly by required distance | Various input cases will be used to track movement of the motors. This will be tested to ensure correct communication between board and device. | Untested | All
3.2.1.3. | Heated Bed Temperature | Can reach 220°C | Use infrared thermometer to check surface temperature. | Untested | All
3.2.1.3. | Hotend Temperature | Can reach 80°C | Use infrared thermometer to check surface temperature. | Untested | All
3.2.2.1. | Extruder Location | Can reach the full printing area of 220x220x250 (mm) | Set extrusion nozzle head to every possible coordinate. | Untested | All

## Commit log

2023-01-26 Add files via upload
    Version 00 of Stepper Motor Driver PCB and Control PCB
    [Axis Driver PCB.PcbDoc, Extruder Stepper Motor Driver.SchDoc, Stepper Motor Driver Board.SchDoc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]
2023-04-20 Create 3D Printer MCU Program
2023-04-26 Update 3D Printer MCU Program
